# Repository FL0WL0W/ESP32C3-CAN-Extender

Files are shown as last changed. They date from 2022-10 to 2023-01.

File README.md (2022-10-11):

# ESP32C3 CAN Extender

This module uses an ESP32C3 with WiFi and BLE. 
It has 3 configurable outputs (5V push pull, Open Drain, 12V pullup), 4 analog or digital inputs, CAN transceiver, 
and an automotive power supply so it can be installed directly into a vehicle. It can be programmed and debugged using the edge connector that connects to any standard 
USBC cable. If you decide to order a PCB yourself, make sure to order it as 0.6mm thickness so that the PCB will fit in the USBC connector.
<br/><br/>
The purpose of this module will be to add cruise control, AC control, tachometer output, speedometer output, and fuel consumption output to my LS3 swapped BMW E30.
The LS3 is currently controlled by the stock GM E38 PCM. This PCM (Powertrain Control Module) uses the CAN bus for the aforementioned items, and this is meant to be a bridge from CAN, to 
discrete signals. This job is originally handled by the BCM (Body Control Module), However the BCM includes alot of items that are not needed for a typical swap, and there 
is not very good documentation on the various BCMs available in cars (compatibility, pinout, etc.). In the future, this car will run on an 
<a href="https://github.com/FL0WL0W/EFIGenie">EFIGenie</a> PCM once the software is more mature. This module will then be useful as a CAN extension module.
<br/><br/>
A demo program will be added soon that has all of the aforementioned features hardcoded, but the eventual goal is to utilize the work from my other repositories 
to create a configurable module that can be programmed through a web UI for various tasks. Another potential feature would be to implement an emulation of the ubiquitous ELM327 bluetooth module that can be used to connect to a phone or tablet to read diagnostic codes, read sensors, or create a digital dash.
<br/><br/>
A 3d model of the enclosure will be uploaded soon as well. The plan is to epoxy pot the pcb inside the enclosure to make it waterproof.




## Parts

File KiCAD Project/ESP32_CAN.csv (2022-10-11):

Source: | C:\Users\johnsond\Documents\KiCad\ESP32_CAN\ESP32_CAN\ESP32_CAN.kicad_sch
Date: | 9/16/2022 11:53
Tool: | Eeschema (6.0.2)
Generator: | C:\Program Files\KiCad\6.0\bin\scripting\plugins/bom_csv_grouped_by_value.py
Component Count: | 72
Individual Components:
Item | Qty | Reference(s) | Value | LibPart | Footprint | Datasheet
 |  | C1 | 100μ | Device:C_Polarized_US | Capacitor_SMD:CP_Elec_10x10.5 | ~
 |  | C2 | 10n | Device:C | Capacitor_SMD:C_0603_1608Metric_Pad1.08x0.95mm_HandSolder | ~
 |  | C3 | 10n | Device:C | Capacitor_SMD:C_0603_1608Metric_Pad1.08x0.95mm_HandSolder | ~
 |  | C4 | 10n | Device:C | Capacitor_SMD:C_0603_1608Metric_Pad1.08x0.95mm_HandSolder | ~
 |  | C5 | 10n | Device:C | Capacitor_SMD:C_0603_1608Metric_Pad1.08x0.95mm_HandSolder | ~
 |  | C6 | 1000μ | Device:C_Polarized_US | Capacitor_SMD:CP_Elec_10x10.5 | ~
 |  | C7 | 10n | Device:C | Capacitor_SMD:C_0603_1608Metric_Pad1.08x0.95mm_HandSolder | ~
 |  | C8 | 10n | Device:C | Capacitor_SMD:C_0603_1608Metric_Pad1.08x0.95mm_HandSolder | ~
 |  | C9 | 10μ | Device:C_Polarized_US | Capacitor_SMD:C_0603_1608Metric_Pad1.08x0.95mm_HandSolder | ~
 |  | C10 | 10n | Device:C | Capacitor_SMD:C_0603_1608Metric_Pad1.08x0.95mm_HandSolder | ~
 |  | C11 | 0.1μ | Device:C | Capacitor_SMD:C_0603_1608Metric_Pad1.08x0.95mm_HandSolder | ~
 |  | C12 | 1μ | Device:C | Capacitor_SMD:C_0603_1608Metric_Pad1.08x0.95mm_HandSolder | ~
 |  | C13 | 100μ | Device:C_Polarized_US | Capacitor_SMD:CP_Elec_10x10.5 | ~
 |  | C14 | 1μ | Device:C | Capacitor_SMD:C_0603_1608Metric_Pad1.08x0.95mm_HandSolder | ~
 |  | C15 | 0.1μ | Device:C | Capacitor_SMD:C_0603_1608Metric_Pad1.08x0.95mm_HandSolder | ~
 |  | C16 | 10n | Device:C | Capacitor_SMD:C_0603_1608Metric_Pad1.08x0.95mm_HandSolder | ~
 |  | C17 | 10n | Device:C | Capacitor_SMD:C_0603_1608Metric_Pad1.08x0.95mm_HandSolder | ~
 |  | C18 | 10n | Device:C | Capacitor_SMD:C_0603_1608Metric_Pad1.08x0.95mm_HandSolder | ~
 |  | C19 | 10n | Device:C | Capacitor_SMD:C_0603_1608Metric_Pad1.08x0.95mm_HandSolder | ~
 |  | D1 | D_Schottky | Device:D_Schottky | Diode_SMD:D_SOD-123 | ~
 |  | D2 | D_Schottky | Device:D_Schottky | Diode_SMD:D_SOD-123 | ~
 |  | D3 | 51V | Device:D_Zener | Diode_SMD:D_SOD-123 | ~
 |  | D4 | 51V | Device:D_Zener | Diode_SMD:D_SOD-123 | ~
 |  | D5 | 51V | Device:D_Zener | Diode_SMD:D_SOD-123 | ~
 |  | D6 | 51V | Device:D_Zener | Diode_SMD:D_SOD-123 | ~
 |  | D7 | 3.3V | Device:D_Zener | Diode_SMD:D_SOD-123 | ~
 |  | D8 | 3.3V | Device:D_Zener | Diode_SMD:D_SOD-123 | ~
 |  | D9 | 3.3V | Device:D_Zener | Diode_SMD:D_SOD-123 | ~
 |  | D10 | 3.3V | Device:D_Zener | Diode_SMD:D_SOD-123 | ~
 |  | D11 | D_Schottky | Device:D_Schottky | Diode_SMD:D_SOD-123 | ~
 |  | J1 | Conn_01x18_Male | Connector:Conn_01x18_Male | MX23A:MX23A18NF1 | ~
 |  | J2 | USB_C_Receptacle_USB2.0 | Connector:USB_C_Receptacle_USB2.0 | USBC:USB_TYPE_C_DS_5 | https://www.usb.org/sites/default/files/documents/usb_type-c.zip
 |  | L1 | 100μ | Device:L | Inductor_SMD:L_12x12mm_H4.5mm | ~
 |  | Q1 | DNI | Transistor_FET_cont:BSS84AKW | Package_TO_SOT_SMD:SOT-323_SC-70_Handsoldering | https://assets.nexperia.com/documents/data-sheet/BSS84AKW.pdf
 |  | Q2 | BSS138BKW | Transistor_FET_cont:BSS138BKW | Package_TO_SOT_SMD:SOT-323_SC-70_Handsoldering | https://assets.nexperia.com/documents/data-sheet/BSS138BKW.pdf
 |  | Q3 | DNI | Transistor_FET_cont:BSS84AKW | Package_TO_SOT_SMD:SOT-323_SC-70_Handsoldering | https://assets.nexperia.com/documents/data-sheet/BSS84AKW.pdf
 |  | Q4 | BSS138BKW | Transistor_FET_cont:BSS138BKW | Package_TO_SOT_SMD:SOT-323_SC-70_Handsoldering | https://assets.nexperia.com/documents/data-sheet/BSS138BKW.pdf
 |  | Q5 | BSS138BKW | Transistor_FET_cont:BSS138BKW | Package_TO_SOT_SMD:SOT-323_SC-70_Handsoldering | https://assets.nexperia.com/documents/data-sheet/BSS138BKW.pdf
 |  | Q6 | DNI | Transistor_FET_cont:BSS84AKW | Package_TO_SOT_SMD:SOT-323_SC-70_Handsoldering | https://assets.nexperia.com/documents/data-sheet/BSS84AKW.pdf
 |  | Q7 | BSS138BKW | Transistor_FET_cont:BSS138BKW | Package_TO_SOT_SMD:SOT-323_SC-70_Handsoldering | https://assets.nexperia.com/documents/data-sheet/BSS138BKW.pdf
 |  | R1 | 4.75K | Device:R_US | Resistor_SMD:R_0603_1608Metric_Pad0.98x0.95mm_HandSolder | ~
 |  | R2 | 4.75K | Device:R_US | Resistor_SMD:R_0603_1608Metric_Pad0.98x0.95mm_HandSolder | ~
 |  | R3 | DNI | Device:R_US | Resistor_SMD:R_0603_1608Metric_Pad0.98x0.95mm_HandSolder | ~
 |  | R4 | 10K | Device:R_US | Resistor_SMD:R_0603_1608Metric_Pad0.98x0.95mm_HandSolder | ~
 |  | R5 | DNI | Device:R_US | Resistor_SMD:R_0603_1608Metric_Pad0.98x0.95mm_HandSolder | ~
 |  | R6 | 10K | Device:R_US | Resistor_SMD:R_0603_1608Metric_Pad0.98x0.95mm_HandSolder | ~
 |  | R7 | 10K | Device:R_US | Resistor_SMD:R_0603_1608Metric_Pad0.98x0.95mm_HandSolder | ~
 |  | R8 | DNI | Device:R_US | Resistor_SMD:R_0603_1608Metric_Pad0.98x0.95mm_HandSolder | ~
 |  | R9 | 10K | Device:R_US | Resistor_SMD:R_0603_1608Metric_Pad0.98x0.95mm_HandSolder | ~
 |  | R10 | 4.75K | Device:R_US | Resistor_SMD:R_0603_1608Metric_Pad0.98x0.95mm_HandSolder | ~
 |  | R11 | 4.75K | Device:R_US | Resistor_SMD:R_0603_1608Metric_Pad0.98x0.95mm_HandSolder | ~
 |  | R12 | 4.75K | Device:R_US | Resistor_SMD:R_0603_1608Metric_Pad0.98x0.95mm_HandSolder | ~
 |  | R13 | 4.75K | Device:R_US | Resistor_SMD:R_0603_1608Metric_Pad0.98x0.95mm_HandSolder | ~
 |  | R14 | DNI | Device:R_US | Resistor_SMD:R_0603_1608Metric_Pad0.98x0.95mm_HandSolder | ~
 |  | R15 | DNI | Device:R_US | Resistor_SMD:R_0603_1608Metric_Pad0.98x0.95mm_HandSolder | ~
 |  | R16 | DNI | Device:R_US | Resistor_SMD:R_0603_1608Metric_Pad0.98x0.95mm_HandSolder | ~
 |  | R17 | DNI | Device:R_US | Resistor_SMD:R_0603_1608Metric_Pad0.98x0.95mm_HandSolder | ~
 |  | R18 | 10K | Device:R_US | Resistor_SMD:R_0603_1608Metric_Pad0.98x0.95mm_HandSolder | ~
 |  | R19 | 10K | Device:R_US | Resistor_SMD:R_0603_1608Metric_Pad0.98x0.95mm_HandSolder | ~
 |  | R20 | 10K | Device:R_US | Resistor_SMD:R_0603_1608Metric_Pad0.98x0.95mm_HandSolder | ~
 |  | R21 | 10K | Device:R_US | Resistor_SMD:R_0603_1608Metric_Pad0.98x0.95mm_HandSolder | ~
 |  | R22 | 10K | Device:R_US | Resistor_SMD:R_0603_1608Metric_Pad0.98x0.95mm_HandSolder | ~
 |  | R23 | DNI | Device:R_US | Resistor_SMD:R_0603_1608Metric_Pad0.98x0.95mm_HandSolder | ~
 |  | R24 | DNI | Device:R_US | Resistor_SMD:R_0603_1608Metric_Pad0.98x0.95mm_HandSolder | ~
 |  | R25 | DNI | Device:R_US | Resistor_SMD:R_0603_1608Metric_Pad0.98x0.95mm_HandSolder | ~
 |  | R26 | DNI | Device:R_US | Resistor_SMD:R_0603_1608Metric_Pad0.98x0.95mm_HandSolder | ~
 |  | RV1 | Varistor | Device:Varistor | Varistor:RV_Disc_D15.5mm_W3.9mm_P7.5mm | ~
 |  | U1 | ATA6561-GAQW-N | Microchip:ATA6561-GAQW-N | Microchip:ATA6561-GAQW-N
 |  | U2 | LM2576S-5 | Regulator_Switching:LM2576S-5 | Package_TO_SOT_SMD:TO-263-5_TabPin3 | http://www.ti.com/lit/ds/symlink/lm2576.pdf
 |  | U3 | AMS1117-3.3 | Regulator_Linear:AMS1117-3.3 | Package_TO_SOT_SMD:SOT-223-3_TabPin2 | http://www.advanced-monolithic.com/pdf/ds1117.pdf
 |  | U4 | BD5230G-TR | TI:TPS3840DL18DBVR | TI:TPS3840DL18DBVR
 |  | U5 | ESP32-C3-MINI-1 | Espressif:ESP32-C3-MINI-1 | Espressif:ESP32-C3-MINI-1 | https://www.espressif.com/sites/default/files/documentation/esp32-c3-mini-1_datasheet_en.pdf
Collated Components:
Item | Qty | Reference(s) | Value | LibPart | Footprint | Datasheet | Cost Each | Cost Total
1 | 2 | C1, C13 | 100μ | Device:C_Polarized_US | Capacitor_SMD:CP_Elec_10x10.5 | ~ | 0.654 | 1.308
2 | 11 | C2, C3, C4, C5, C7, C8, C10, C16, C17, C18, C19 | 10n | Device:C | Capacitor_SMD:C_0603_1608Metric_Pad1.08x0.95mm_HandSolder | ~ | 0.006 | 0.066
3 | 1 | C6 | 1000μ | Device:C_Polarized_US | Capacitor_SMD:CP_Elec_10x10.5 | ~ | 0.767 | 0.767
4 | 1 | C9 | 10μ | Device:C_Polarized_US | Capacitor_SMD:C_0603_1608Metric_Pad1.08x0.95mm_HandSolder | ~ | 0.025 | 0.025
5 | 2 | C11, C15 | 0.1μ | Device:C | Capacitor_SMD:C_0603_1608Metric_Pad1.08x0.95mm_HandSolder | ~ | 0.005 | 0.01
6 | 2 | C12, C14 | 1μ | Device:C | Capacitor_SMD:C_0603_1608Metric_Pad1.08x0.95mm_HandSolder | ~ | 0.014 | 0.028
7 | 3 | D1, D2, D11 | D_Schottky | Device:D_Schottky | Diode_SMD:D_SOD-123 | ~ | 0.364 | 1.092
8 | 4 | D3, D4, D5, D6 | 51V | Device:D_Zener | Diode_SMD:D_SOD-123 | ~ | 0.223 | 0.892
9 | 4 | D7, D8, D9, D10 | 3.3V | Device:D_Zener | Diode_SMD:D_SOD-123 | ~ | 0.082 | 0.328
10 | 1 | J1 | Conn_01x18_Male | Connector:Conn_01x18_Male | MX23A:MX23A18NF1 | ~ | 5 | 5
11 | 1 | J2 | USB_C_Receptacle_USB2.0 | Connector:USB_C_Receptacle_USB2.0 | USBC:USB_TYPE_C_DS_5 | https://www.usb.org/sites/default/files/documents/usb_type-c.zip | 0 | 0
12 | 1 | L1 | 100μ | Device:L | Inductor_SMD:L_12x12mm_H4.5mm | ~ | 0.18 | 0.18
13 | 3 | Q1, Q3, Q6 | DNI | Transistor_FET_cont:BSS84AKW | Package_TO_SOT_SMD:SOT-323_SC-70_Handsoldering | https://assets.nexperia.com/documents/data-sheet/BSS84AKW.pdf | 0.062 | 0.186
14 | 4 | Q2, Q4, Q5, Q7 | BSS138BKW | Transistor_FET_cont:BSS138BKW | Package_TO_SOT_SMD:SOT-323_SC-70_Handsoldering | https://assets.nexperia.com/documents/data-sheet/BSS138BKW.pdf | 0.052 | 0.208
15 | 6 | R1, R2, R10, R11, R12, R13 | 4.75K | Device:R_US | Resistor_SMD:R_0603_1608Metric_Pad0.98x0.95mm_HandSolder | ~ | 0.001 | 0.006
16 | 11 | R3, R5, R8, R14, R15, R16, R17, R23, R24, R25, R26 | DNI | Device:R_US | Resistor_SMD:R_0603_1608Metric_Pad0.98x0.95mm_HandSolder | ~ | 0.002 | 0.022
17 | 9 | R4, R6, R7, R9, R18, R19, R20, R21, R22 | 10K | Device:R_US | Resistor_SMD:R_0603_1608Metric_Pad0.98x0.95mm_HandSolder | ~ | 0.002 | 0.018
18 | 1 | RV1 | Varistor | Device:Varistor | Varistor:RV_Disc_D15.5mm_W3.9mm_P7.5mm | ~ | 0.066 | 0.066
19 | 1 | U1 | ATA6561-GAQW-N | Microchip:ATA6561-GAQW-N | Microchip:ATA6561-GAQW-N |  | 1.77 | 1.77
20 | 1 | U2 | LM2576S-5 | Regulator_Switching:LM2576S-5 | Package_TO_SOT_SMD:TO-263-5_TabPin3 | http://www.ti.com/lit/ds/symlink/lm2576.pdf | 0.2 | 0.2
21 | 1 | U3 | AMS1117-3.3 | Regulator_Linear:AMS1117-3.3 | Package_TO_SOT_SMD:SOT-223-3_TabPin2 | http://www.advanced-monolithic.com/pdf/ds1117.pdf | 0.1 | 0.1
22 | 1 | U4 | BD5230G-TR | TI:TPS3840DL18DBVR | TI:TPS3840DL18DBVR |  | 0.279 | 0.279
23 | 1 | U5 | ESP32-C3-MINI-1 | Espressif:ESP32-C3-MINI-1 | Espressif:ESP32-C3-MINI-1 | https://www.espressif.com/sites/default/files/documentation/esp32-c3-mini-1_datasheet_en.pdf | 1.95 | 1.95
24 | 1 |  | PCB |  |  |  | 2.551 | 2.551
 | 45 |  | Epoxy Potting Compound |  |  |  | 0.08 | 3.6
 |  |  |  |  |  |  |  | 20.652

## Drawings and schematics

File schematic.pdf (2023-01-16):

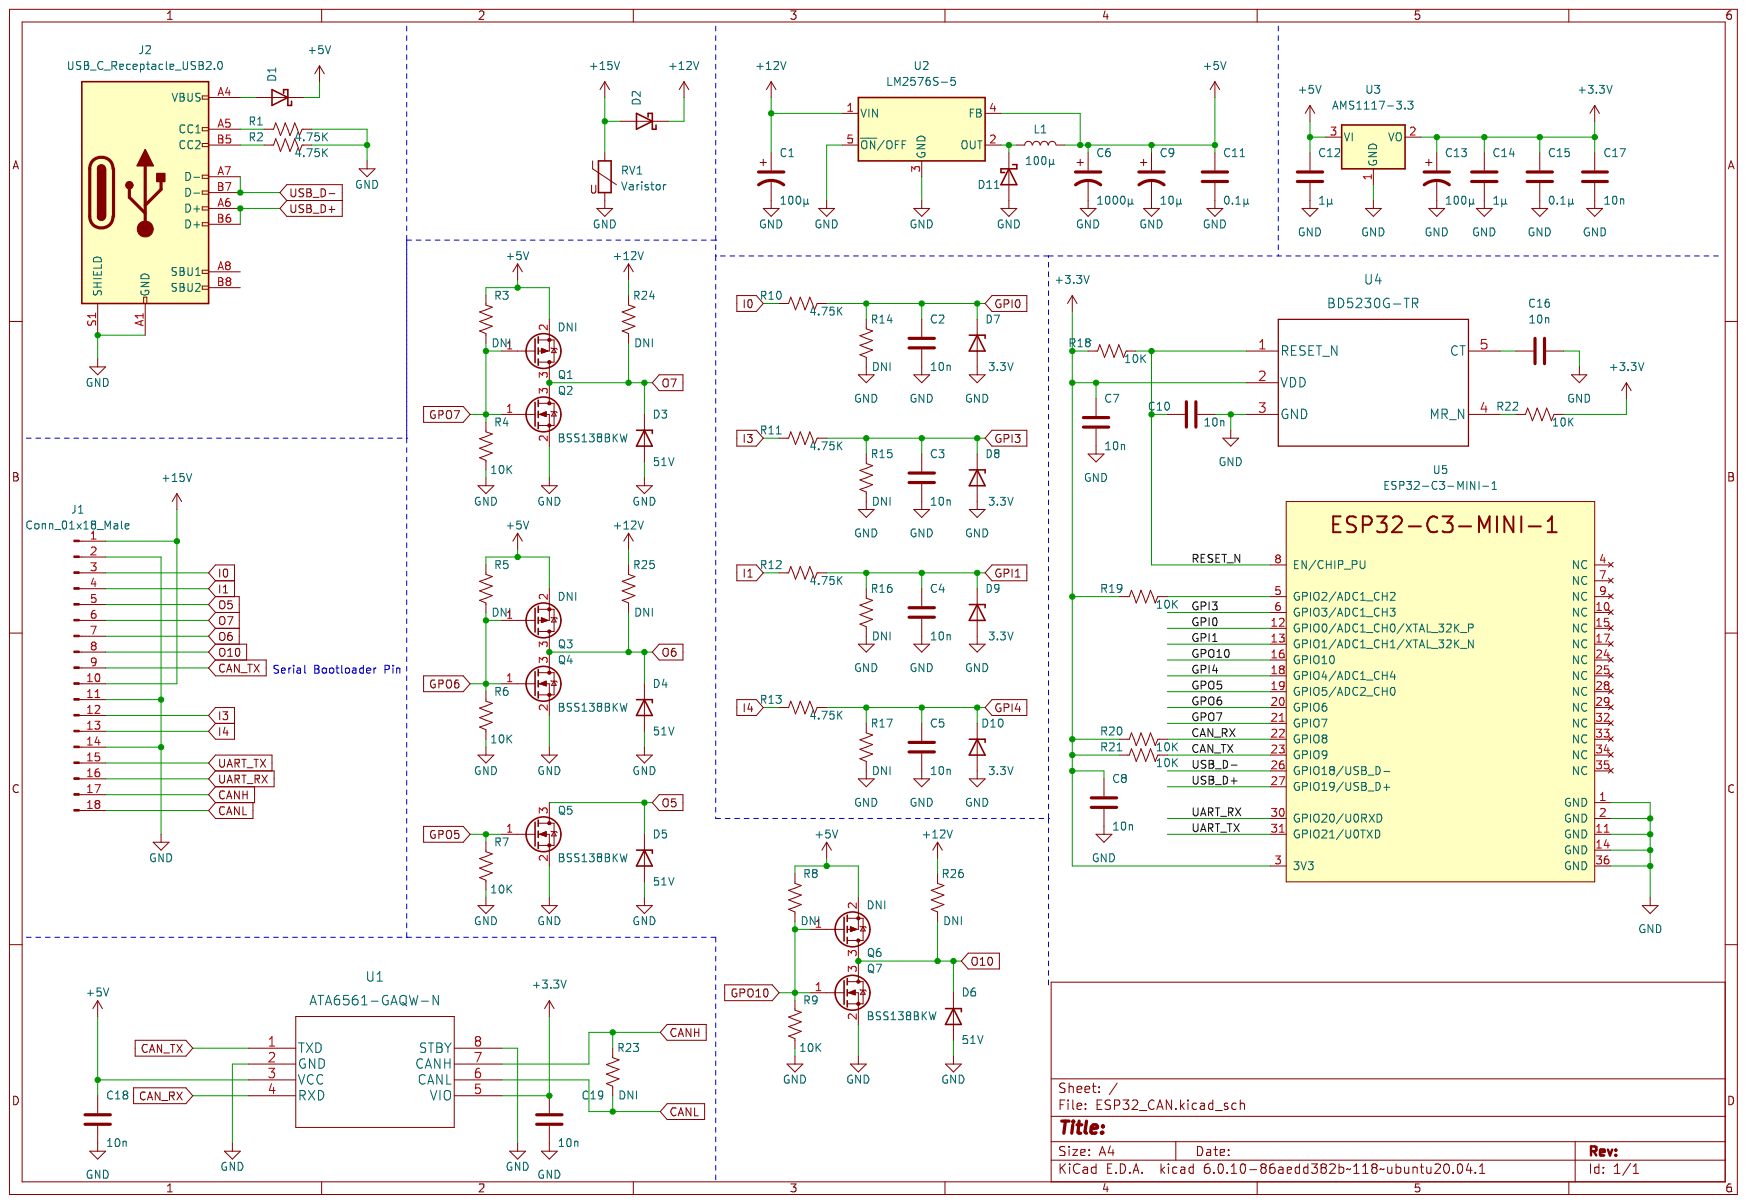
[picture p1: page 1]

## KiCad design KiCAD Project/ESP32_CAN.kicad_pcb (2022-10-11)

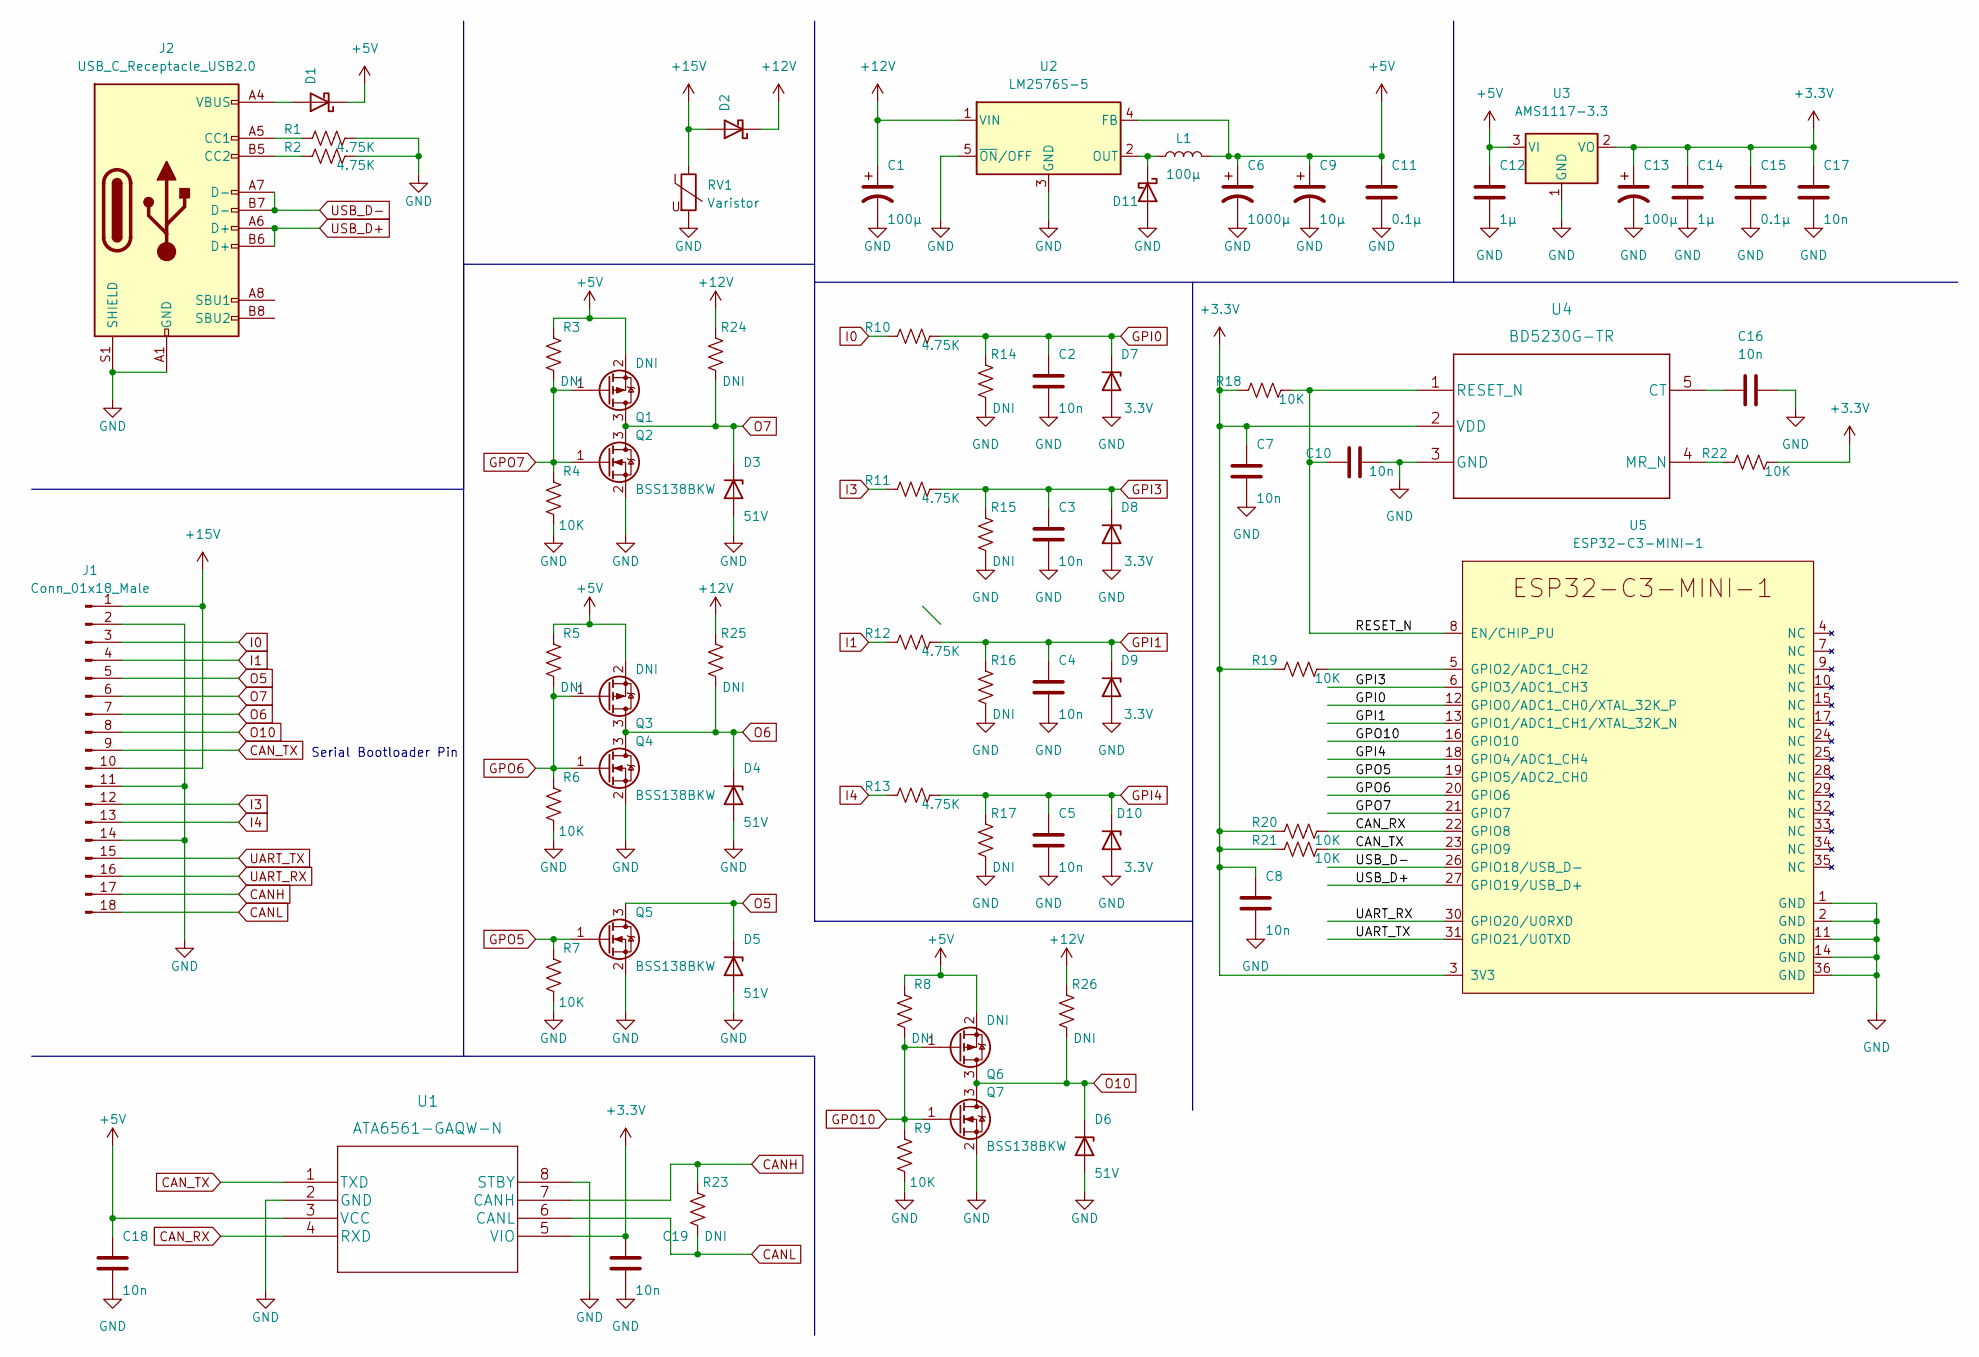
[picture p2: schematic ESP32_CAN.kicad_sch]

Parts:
C1, C13: 100μ; CP_Elec_10x10.5
C2, C3, C4, C5, C7, C8, C10, C16, C17, C18, C19: 10n; C_0603_1608Metric_Pad1.08x0.95mm_HandSolder
C6: 1000μ; CP_Elec_10x10.5
C9: 10μ; C_0603_1608Metric_Pad1.08x0.95mm_HandSolder
C11, C15: 0.1μ; C_0603_1608Metric_Pad1.08x0.95mm_HandSolder
C12, C14: 1μ; C_0603_1608Metric_Pad1.08x0.95mm_HandSolder
D1, D2, D11: D_Schottky; D_SOD-123
D3, D4, D5, D6: 51V; D_SOD-123
D7, D8, D9, D10: 3.3V; D_SOD-123
J1: Conn_01x18_Male; MX23A18NF1
J2: USB_C_Receptacle_USB2.0; USB_TYPE_C_DS_5
L1: 100μ; L_12x12mm_H4.5mm
Q1, Q3, Q6: DNI; SOT-323_SC-70_Handsoldering
Q2, Q4, Q5, Q7: BSS138BKW; SOT-323_SC-70_Handsoldering
R1, R2, R10, R11, R12, R13: 4.75K; R_0603_1608Metric_Pad0.98x0.95mm_HandSolder
R3, R5, R8, R14, R15, R16, R17, R23, R24, R25, R26: DNI; R_0603_1608Metric_Pad0.98x0.95mm_HandSolder
R4, R6, R7, R9, R18, R19, R20, R21, R22: 10K; R_0603_1608Metric_Pad0.98x0.95mm_HandSolder
RV1: Varistor; RV_Disc_D15.5mm_W3.9mm_P7.5mm
U1: ATA6561-GAQW-N
U2: LM2576S-5; TO-263-5_TabPin3
U3: AMS1117-3.3; SOT-223-3_TabPin2
U4: BD5230G-TR; TPS3840DL18DBVR
U5: ESP32-C3-MINI-1

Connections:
+3V3: C7.1, C8.1, C13.1, C14.1, C15.1, C17.1, C19.1, R18.1, R19.1, R20.1, R21.1, R22.2, U1.5 (VIO), U3.2 (VO), U4.2 (VDD), U5.3 (3V3)
+5V: C6.1, C9.1, C11.1, C12.1, C18.1, D1.1 (K), L1.2, Q1.2 (S), Q3.2 (S), Q6.2 (S), R3.2, R5.2, R8.2, U1.3 (VCC), U2.4 (FB), U3.3 (VI)
+12V: C1.1, D2.1 (K), R24.2, R25.2, R26.2, U2.1 (VIN)
+15V: D2.2 (A), J1.1, J1.10, RV1.1
/RESET_N: C10.1, R18.2, U4.1 (RESET_N), U5.8 (EN/CHIP_PU)
CANH: J1.17, R23.2, U1.7 (CANH)
CANL: J1.18, R23.1, U1.6 (CANL)
CAN_RX: R20.2, U1.4 (RXD), U5.22 (GPIO8)
CAN_TX: J1.9, R21.2, U1.1 (TXD), U5.23 (GPIO9)
GND: C1.2, C2.2, C3.2, C4.2, C5.2, C6.2, C7.2, C8.2, C9.2, C10.2, C11.2, C12.2, C13.2, C14.2, C15.2, C16.2, C17.2, C18.2, C19.2, D3.2 (A), D4.2 (A), D5.2 (A), D6.2 (A), D7.2 (A), D8.2 (A), D9.2 (A), D10.2 (A), D11.2 (A), J1.2, J1.11, J1.14, J2.A1 (GND), J2.A12 (GND), J2.B1 (GND), J2.B12 (GND), J2.S1 (SHIELD), Q2.2 (S), Q4.2 (S), Q5.2 (S), Q7.2 (S), R1.2, R2.2, R4.1, R6.1, R7.1, R9.1, R14.1, R15.1, R16.1, R17.1, RV1.2, U1.2 (GND), U1.8 (STBY), U2.3 (GND), U2.5 (~ON/OFF), U3.1 (GND), U4.3 (GND), U5.1 (GND), U5.2 (GND), U5.11 (GND), U5.14 (GND), U5.36 (GND)
GPI0: C2.1, D7.1 (K), R10.2, R14.2, U5.12 (GPIO0/ADC1_CH0/XTAL_32K_P)
GPI1: C4.1, D9.1 (K), R12.2, R16.2, U5.13 (GPIO1/ADC1_CH1/XTAL_32K_N)
GPI3: C3.1, D8.1 (K), R11.2, R15.2, U5.6 (GPIO3/ADC1_CH3)
GPI4: C5.1, D10.1 (K), R13.2, R17.2, U5.18 (GPIO4/ADC1_CH4)
GPO5: Q5.1 (G), R7.2, U5.19 (GPIO5/ADC2_CH0)
GPO6: Q3.1 (G), Q4.1 (G), R5.1, R6.2, U5.20 (GPIO6)
GPO7: Q1.1 (G), Q2.1 (G), R3.1, R4.2, U5.21 (GPIO7)
GPO10: Q6.1 (G), Q7.1 (G), R8.1, R9.2, U5.16 (GPIO10)
I0: J1.3, R10.1
I1: J1.4, R12.1
I3: J1.12, R11.1
I4: J1.13, R13.1
unnamed: C16.1, U4.5 (CT)
unnamed: D1.2 (A), J2.A4 (VBUS), J2.A9 (VBUS), J2.B4 (VBUS), J2.B9 (VBUS)
unnamed: D11.1 (K), L1.1, U2.2 (OUT)
unnamed: J2.A5 (CC1), R1.1
unnamed: J2.B5 (CC2), R2.1
unnamed: R19.2, U5.5 (GPIO2/ADC1_CH2)
unnamed: R22.1, U4.4 (MR_N)
O5: D5.1 (K), J1.5, Q5.3 (D)
O6: D4.1 (K), J1.7, Q3.3 (D), Q4.3 (D), R25.1
O7: D3.1 (K), J1.6, Q1.3 (D), Q2.3 (D), R24.1
O10: D6.1 (K), J1.8, Q6.3 (D), Q7.3 (D), R26.1
UART_RX: J1.16, U5.30 (GPIO20/U0RXD)
UART_TX: J1.15, U5.31 (GPIO21/U0TXD)
USB_D+: J2.A6 (D+), J2.B6 (D+), U5.27 (GPIO19/USB_D+)
USB_D-: J2.A7 (D-), J2.B7 (D-), U5.26 (GPIO18/USB_D-)

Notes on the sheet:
Serial Bootloader Pin

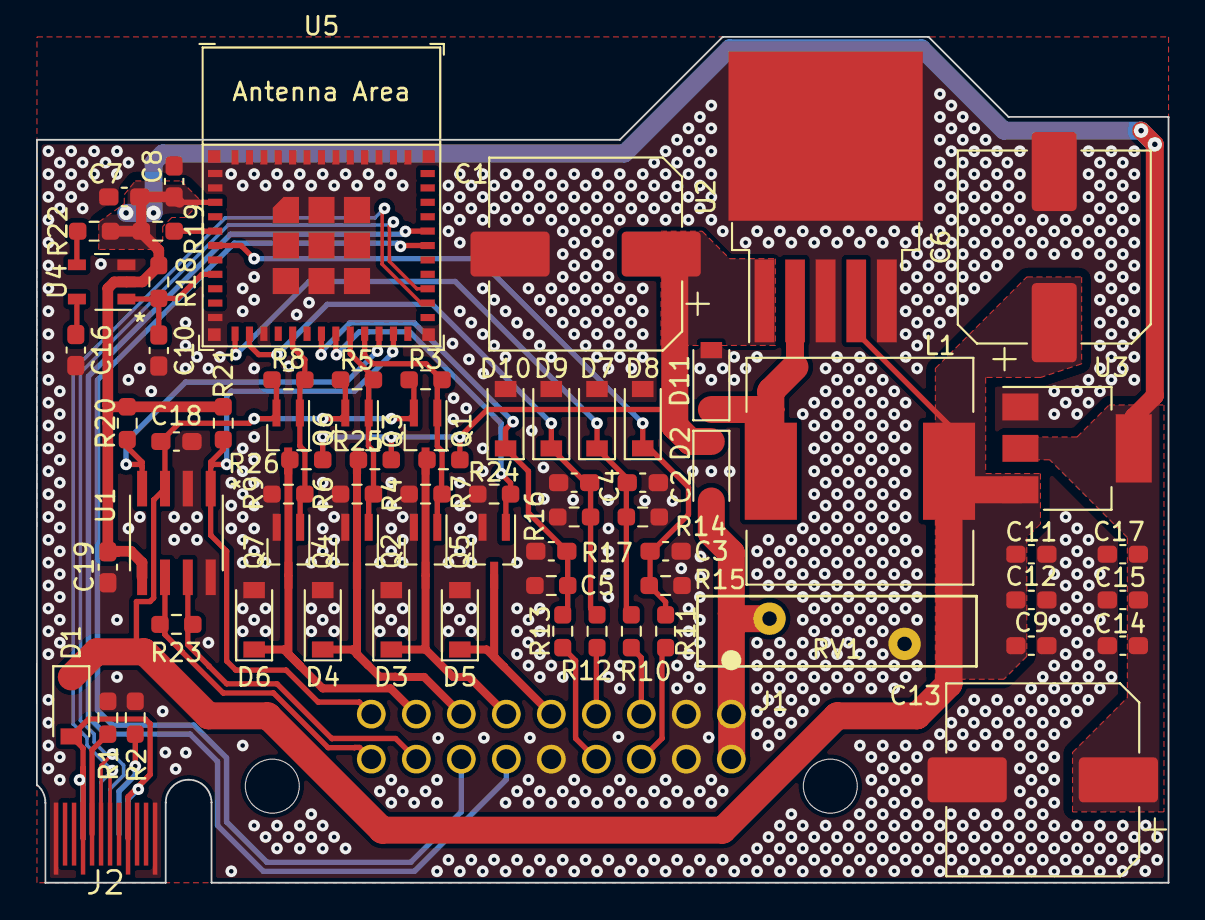
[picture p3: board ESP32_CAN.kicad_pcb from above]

Board: 2 copper layers, 62.9 x 47.0 mm, 72 parts (0 on the bottom side), 37 nets.

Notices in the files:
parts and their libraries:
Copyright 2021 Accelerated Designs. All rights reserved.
